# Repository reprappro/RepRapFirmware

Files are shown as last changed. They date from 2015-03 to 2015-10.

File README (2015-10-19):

This firmware is intended to be a fully object-oriented highly modular control program for
RepRap self-replicating 3D printers.

It owes a lot to Marlin and to the original RepRap FiveD_GCode.

This is the version for the RepRap Duet: 

  http://blog.think3dprint3d.com/2013/12/Duet-Arduino-Due-compatible-3DPrinter-controller.html  

To edit and compile this you will also need the Arduino board files from

  https://github.com/reprappro/RepRapFirmware/tree/master/Hardware

A complete uploadable executable version is in the directory Release/RepRapFirmware.bin in this
repository.  For details of how to flash it to a Duet see here:

  https://reprappro.com/documentation/commissioning-introduction/maintenance-duet/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

For details of how to compile the source code, see below.

General design principles:

  * Control by RepRap G Codes.  These are taken to be machine independent, though some may be unsupported.
  * Full use of C++ OO techniques,
  * Make classes hide their data,
  * Make everything except the Platform class (see below) as stateless as possible,
  * No use of conditional compilation except for #include guards - if you need that, you should be
       forking the repository to make a new branch - let the repository take the strain,
  * Concentration of all machine-dependent definitions and code in Platform.h and Platform.cpp,
  * No specials for (X,Y) or (Z) - all movement is 3-dimensional,
  * Except in Platform.h, use real units (mm, seconds etc) throughout the rest of the code wherever possible,
  * Try to be efficient in memory use, but this is not critical,
  * Labour hard to be efficient in time use, and this is critical,
  * Don't abhor floats - they work fast enough if you're clever,
  * Don't avoid arrays and structs/classes,
  * Don't avoid pointers,
  * Use operator and function overloading where appropriate.

Naming conventions:

  * #defines are all CAPITALS_WITH_OPTIONAL_UNDERSCORES_BETWEEN_WORDS
  * No underscores in other names - MakeReadableWithCapitalisation
  * Class names and functions start with a CapitalLetter
  * Variables start with a lowerCaseLetter
  * Use veryLongDescriptiveNames

Structure:

There are nine main classes:

  * RepRap
  * GCodes
  * Heat
  * Move
  * Platform
  * Network
  * Webserver
  * Roland, and
  * PrintMonitor

RepRap:

  This is just a container class for the single instances of all the others, and otherwise does very little.

GCodes:

  This class is fed GCodes, either from the web interface, or from GCode files, or from a serial interface,
  Interprets them, and requests actions from the RepRap machine via the other classes.

Heat:

  This class implements all heating and temperature control in the RepRap machine.

Move:

  This class controls all movement of the RepRap machine, both along its axes, and in its extruder drives.

Platform:

  This is the only class that knows anything about the physical setup of the RepRap machine and its
  controlling electronics.  It implements the interface between all the other classes and the RepRap machine.
  All the other classes are completely machine-independent (though they may declare arrays dimensioned
  to values #defined in Platform.h).

Network:

  This class implements a basic TCP interface for the Webserver classes using LWIP.

Webserver:

  This class talks to the network (via Platform) and implements a simple webserver to give an interactive
  interface to the RepRap machine. It uses the Knockout and Jquery Javascript libraries to achieve this.
  In addition, FTP and Telnet servers are provided for easier SD card file management and G-Code handling.

Roland:

  This class can interface with a Roland mill (e.g. Roland MDX-20/15) and allows the underlying hardware
  to act as a G-Code proxy, which translates G-Codes to internal Roland commands.

PrintMonitor:

  This class provides methods to obtain statistics (height, filament usage etc.) from generated G-Code
  files and to calculate estimated print end-times for a live print.

When the software is running there is one single instance of each main class, and all the memory allocation is
done on initialization.  new/malloc should not be used in the general running code, and delete is never
used.  Each class has an Init() function that resets it to its boot-up state; the constructors merely handle
that memory allocation on startup.  Calling RepRap.Init() calls all the other Init()s in the right sequence.

There are other ancillary classes that are declared in the .h files for the master classes that use them.  For
example, Move has a DDA class that implements a Bresenham/digital differential analyser.

Timing:

There is a single interrupt chain entered via Platform.Interrupt().  This controls movement step timing, and
this chain of code should be the only place that volatile declarations and structure/variable-locking are
required.  All the rest of the code is called sequentially and repeatedly as follows:

As of version 057r-dc42 the tick interrupt (which is set up by the Arduino core) is also used to set up ADC conversions,
read the result of the last conversion, and shut down heaters when temperature errors are detected.

All the main classes have a Spin() function.  These are called in a loop by the RepRap.Spin() function and implement
simple timesharing.  No class does, or ever should, wait inside one of its functions for anything to happen or call
any sort of delay() function.  The general rule is:

  Can I do a thing?
    Yes - do it
    No - set a flag/timer to remind me to do it next-time-I'm-called/at-a-future-time and return.

The restriction this strategy places on almost all the code in the firmware (that it must execute quickly and
never cause waits or delays) is balanced by the fact that none of that code needs to worry about synchronization,
locking, or other areas of code accessing items upon which it is working.  As mentioned, only the interrupt
chain needs to concern itself with such problems.  Unlike movement, heating (including PID controllers) does
not need the fast precision of timing that interrupts alone can offer.  Indeed, most heating code only needs
to execute a couple of times a second.

Most data is transferred bytewise, with classes' Spin() functions typically containing code like this:

  Is a byte available for me?
    Yes
      read it and add it to my buffer
      Is my buffer complete?
         Yes
           Act on the contents of my buffer
         No
           Return
  No
    Return

Note that it is simple to raise the "priority" of any class's activities relative to the others by calling its
Spin() function more than once from RepRap.Spin().

-------------

Compiling from Source

Although the firmware was originally developed using Eclipse Juno, the latest version of the Arduino toolkit (1.6.4) breaks compatibility
with the Arduino Eclipse Plugin. Hence a Makefile has been introduced to compile the firmware easily on OS X and Linux. For Windows there
is also a Windows PowerShell script available.

As a prerequisite you must install Arduino IDE and the necessary board files. Refer to the README file in the Hardware directory for
basic instructions on how this can be achieved.

Compiling the firmware is fairly easy on *nix-based operating systems. All you need to do is to run

  make all

in the source code folder. On Windows, you can use the corresponding PowerShell script instead:

  powershell.exe -ExecutionPolicy Unrestricted -FileName .\Make.ps1

Once a firmware binary has been generated, both Makefiles can be further used to upload the generated output file to the erased electronics
board:

  make upload

or on Windows

  powershell.exe -ExecutionPolicy Unrestricted -FileName .\Make.ps1 upload

In order to take advantage of more sophisticated development conditions, a clang configuration file is included in this directory. It may be used,
for example, with vim-clang. If you decide to use it, just don't forget to set your clang C options to '-std=gnu99' and your CPP flags to '-std=gnu++11'.

-------------
Note on dc42 fork of this firmware:

As well as containing various bug fixes and performance improvements, I have added various functionality compared to the original RepRapPro version.
The major changes are:

- Z probe reading is included in the web server poll response
- Homed status (i.e. whether homes since reset) is maintained for all 3 axes and included in the web server poll response
- Once the X and Y axes have been homed, movement is limited to the range of the axis, except when the G0 or G1 command includes
  the check endstops (S1) parameter. Use the M208 command to set axis travel if the default values in the firmware are incorrect for your machine.
- Implemented M301 (hot end PID parameters) and M304 (bed PID parameters) commands. Extended these commands to allow setting of thermistor
  resistance at 25C (R parameter) and thermistor beta (B parameter). A negative P parameter means don't use PID, use bang-bang control.
- Implemented M999. This resets the Duet.
- Added temperature (T) and temperature coefficient of height (C) parameters to the G31 command
- Added support for modulated IR sensor (M558 P2) and ultrasonic sensor (M558 P3)
- Various parameters are now saved to flash memory (Z-probe parameters, network parameters, PID parameters)
- FAN0 line is driven at 25kHz and pin 25 on the expansion header (Duet) can utilise the tacho line of 4-pin PWM fans

-------------
Note on zpl fork of this firmware:

Based on dc42's long-time proven Duet firmware fork, I have implemented a couple more features and (partially) merged in features from RepRapPro's development firmware branch.
The most significant changes are:

- FTP and Telnet support
- Reliable low-level networking and implementation of the internal EMAC ISR
- Internal G-Code queuing to execute non-movement codes just-in-time and not ~20 moves too early (due to the look-ahead)
- M25: SD-card prints are paused as soon as the current move finishes
- M0 does no longer disable any stepper motors or heaters if the print is paused. This shall simplify print restarts (requires my web interface fork)
- Implemented cold retracts, minimum temperature is 90C
- Flash usage is optional; only one line needs to be commented out to disable it

See the "Changes in ... fork" text files for complete lists of all the changes dc42 and zpl have contributed.

-------------

Version 1.09

Started: 2012-11-18
This README dated: 2015-10-14

Adrian Bowyer
RepRap Professional Ltd
http://reprappro.com

Licence: GPL

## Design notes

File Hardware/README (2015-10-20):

Custom hardware tree for the Duet platform (version 1.0.4)

This tree is based upon the official "Arduino Due" 1.6.5 platform files, however the following changes were made:

- WString class is no longer present in the Arduino core. Use char arrays in conjunction with StringRef containers instead
- EMAC RX buffers were increased to 128*32 for optimal network performance
- UART classes were expanded by a "canWrite" method for better sending performance

To include this hardware tree, open the Arduino IDE.  Open the Boards Manager and install the Due device tree.  Then
go to File -> Preferences and set "Additional Boards Manager URLs" to:

  https://github.com/reprappro/RepRapFirmware/raw/dev/Hardware/package_reprap_index.json
  
Then open the Boards Manager and install the Duet device tree.

All of these files are licensed under the terms and conditions of the GPL.

Many thanks to David Crocker aka dc42 for providing the initial Arduino core patches
and to Tony@T3P3 for providing the necessary changes for their new Duet 0.8.5!

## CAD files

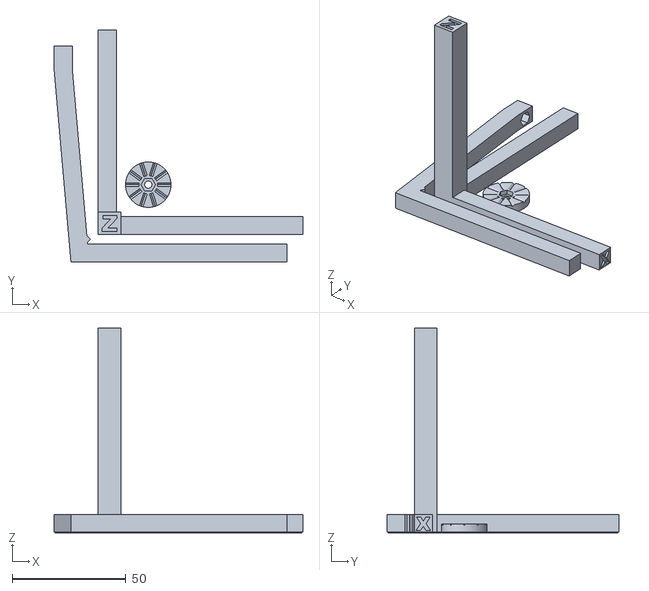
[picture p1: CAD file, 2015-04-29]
STL/calibration_90mm.stl
109.4 x 102.0 x 90.0

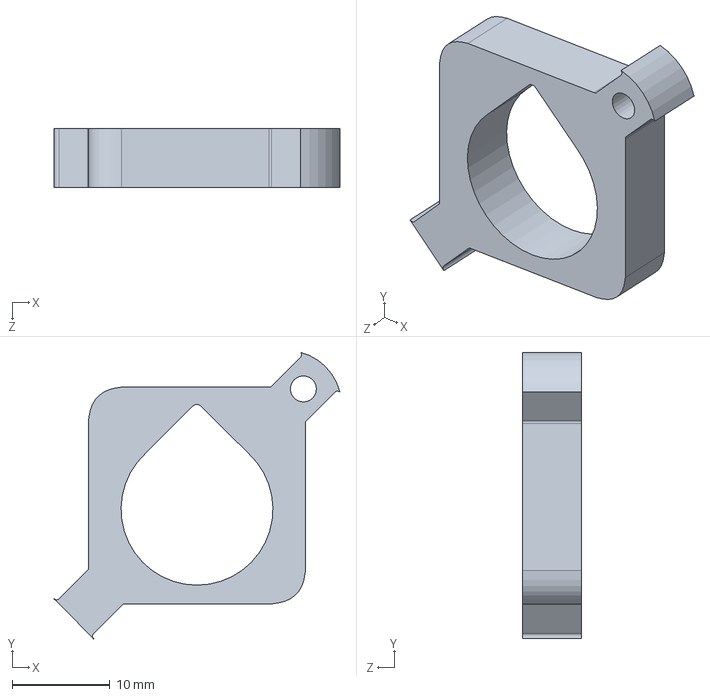
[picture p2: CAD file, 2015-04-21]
STL/Dual-colour-logo-keyring/rrp-logo-block.SLDPRT
29.3 x 29.3 x 6.00 mm

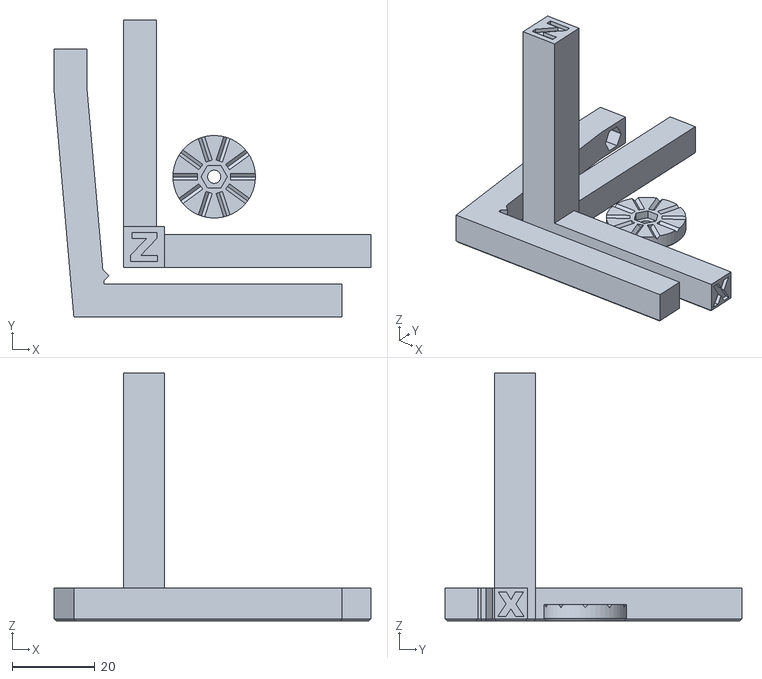
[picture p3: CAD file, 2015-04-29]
STL/calibration_60mm.stl
76.8 x 72.0 x 60.0

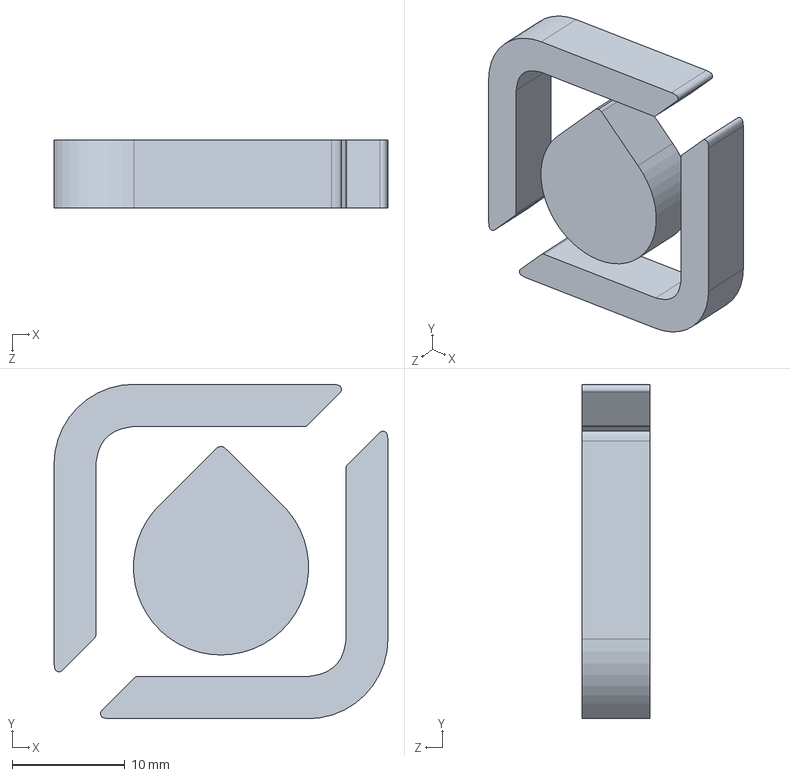
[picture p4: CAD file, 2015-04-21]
STL/Dual-colour-logo-keyring/rrp-logo.SLDPRT
29.6 x 29.7 x 6.00 mm

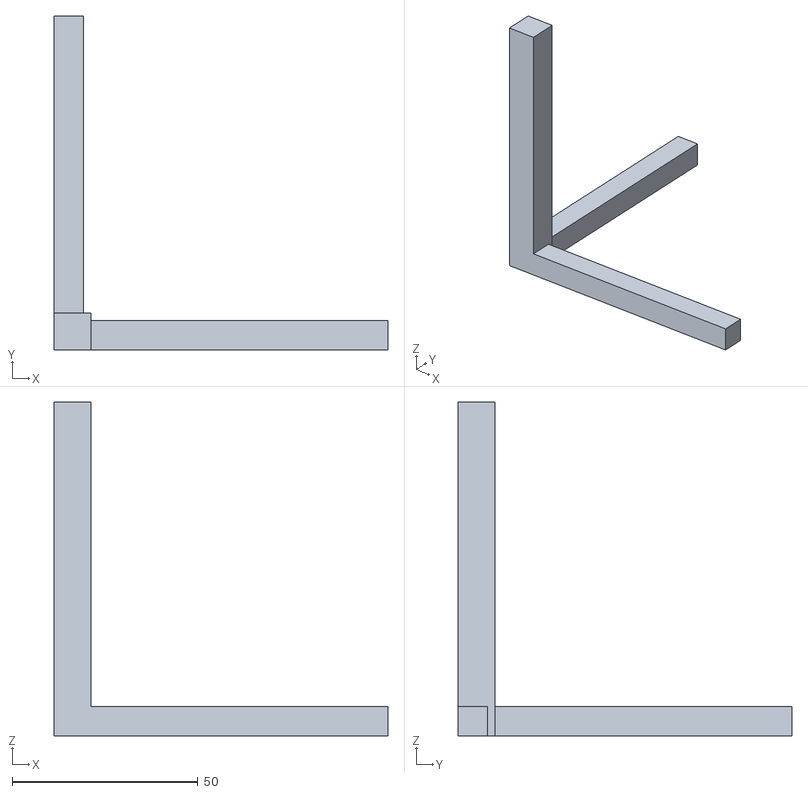
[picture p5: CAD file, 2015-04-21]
STL/testpiece_90mm.stl
90.0 x 90.0 x 90.0

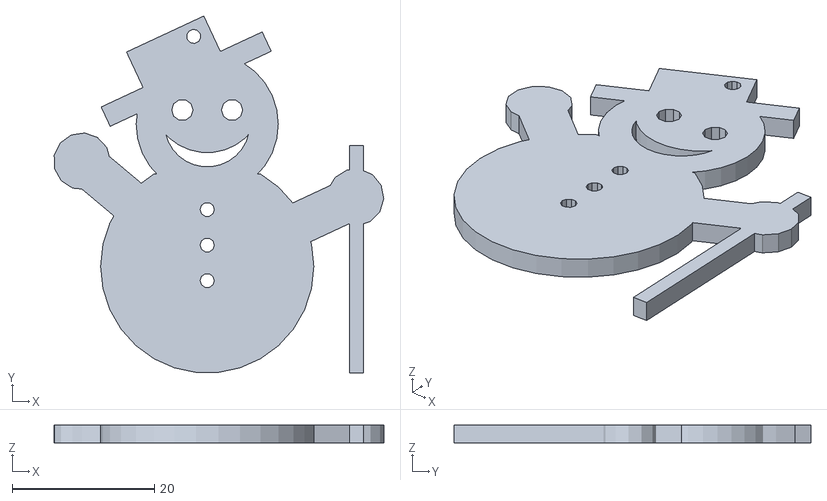
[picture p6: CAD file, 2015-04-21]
STL/Snowman.stl
46.4 x 50.2 x 2.50

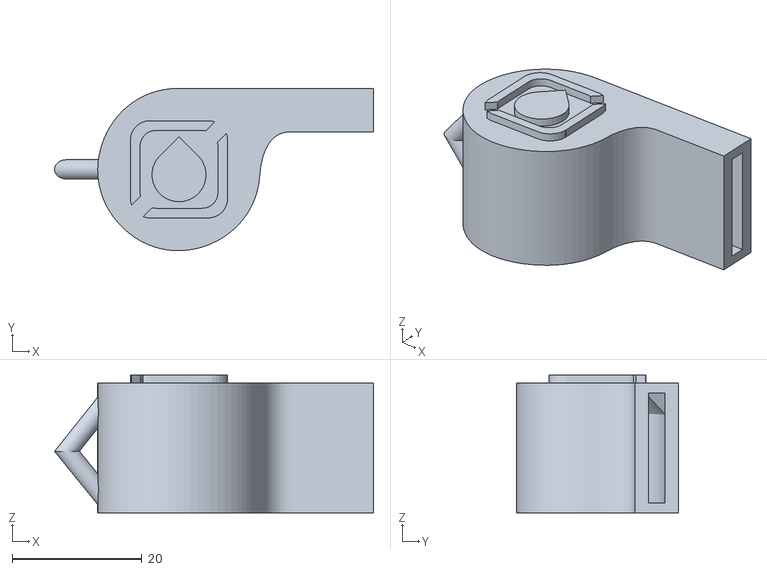
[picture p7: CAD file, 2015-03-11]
STL/Whistle.stl
49.2 x 25.0 x 21.2

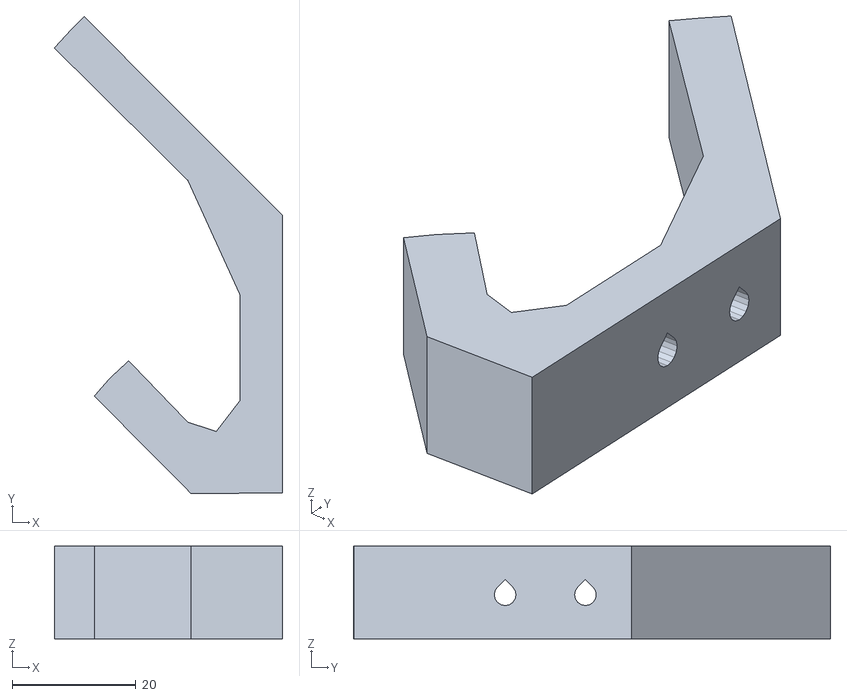
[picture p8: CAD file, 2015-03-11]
STL/CoatHook.stl
36.9 x 77.1 x 15.0

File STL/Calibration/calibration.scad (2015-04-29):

// OpenSCAD file for producing the testpiece, gauge and thumbwheel for orthogonal axis compensation for RepRapPro Ormerod, Mendel and Huxley printers //
// Revised with text. You need to use OpenSCAD version 2015.03 for the test to render correctly, and Arial Black installed as a font //

long = 90; // Set length for testpiece here
chamfer=0.5;

// comment out the following lines to get the parts you want. Comment out the translations if you want the part at the origin.

Gauge();

translate ([12,12,0])
TestPiece();

translate ([34,34,0])
ThumbWheel();



module Gauge()
{
    union()
     {
         chamfer_cube(long+5,8,8);
         translate([5, 10, 4]) rotate([0,0,45]) chamfer_cube(5,5,8,ctr=true);
         
         difference ()
         {
             rotate([0,0,5]) chamfer_cube(8,long,8);
             translate ([-sin(5)*(long-5)-1,(long-5),-1]) cube([10,11,10]);
         }
         
         translate ([-sin(5)*(long-5),(long-5),0]) difference ()
         {
             chamfer_cube(8,10,8,x1=false);
             translate([4,5,4]) rotate([0,90,0]) cylinder(r=1.6,h=10,center=true,$fn=30);
             translate([4,5,4]) rotate([90,0,90]) cylinder(r=3.2,h=6,center=false,$fn=6);
         }
     }
}

module ThumbWheel()
{
	difference()
	{
		intersection ()
		{
			cylinder(r=10,h=4,center=false,$fn=50);
			cylinder(r1=10-chamfer,r2=10+4-chamfer,h=4,center=false,$fn=50);
		}
		translate ([0,0,-1]) cylinder(r=1.6,h=6,center=false,$fn=30);
		translate ([0,0,-0.02]) cylinder(r1=1.6+chamfer,r2=1.6,h=chamfer,center=false,$fn=30);
		translate([0,0,2]) cylinder(r=3.2,h=3,center=false,$fn=6);

		for(a = [0 : 36 : 360] )
		{
		rotate([0,0,a]) translate([4,0,3.2]) rotate([45,0,0])
            cube([7,1.5,1.5]);
		}
	}
}


module TestPiece()
{
 union()
 {
	difference ()
     {
         chamfer_cube(long,8,8);
         translate ([long-1,0.75,1]) rotate ([90,0,90]) 
         linear_extrude(height = 1.1) text("X", font="Arial Black", size=6);
     }

	difference ()
     {
         chamfer_cube(8,long,8);
         translate ([0.75,long+0.1,1]) rotate ([90,0,0]) 
         linear_extrude(height = 1.1) text("Y", font="Arial Black", size=6);
     }

	difference ()
     {
         chamfer_cube(10,10,long);
         translate ([1.5,1.5,long-1]) 
         linear_extrude(height = 1.1) text("Z", font="Arial Black", size=7);
     }


 }
}

module chamfer_cube (x,y,z,h=chamfer,ctr=false,x1=true,x2=true,y1=true,y2=true)
{
    dh = sqrt(2*pow(h,2));

	if (ctr==true)
    {
        translate ([-x/2,-y/2,-z/2]) difference ()
        {
            cube([x,y,z]);
            if (x1==true) {translate([x/2,-0.02,-0.02]) rotate ([45,0,0]) cube([x+1,dh,dh],center=true);}
            if (x2==true) {translate([x/2,y+0.02,-0.02]) rotate ([45,0,0]) cube([x+1,dh,dh],center=true);}
            if (y1==true) {translate([-0.02,y/2,-0.02]) rotate ([0,45,0]) cube([dh,y+1,dh],center=true);}
            if (y2==true) {translate([x+0.02,y/2,-0.02]) rotate ([0,45,0]) cube([dh,y+1,dh],center=true);}
        }
    }
    else
    {
        difference ()
        {
            cube([x,y,z]);
            if (x1==true) {translate([x/2,-0.02,-0.02]) rotate ([45,0,0]) cube([x+1,dh,dh],center=true);}
            if (x2==true) {translate([x/2,y+0.02,-0.02]) rotate ([45,0,0]) cube([x+1,dh,dh],center=true);}
            if (y1==true) {translate([-0.02,y/2,-0.02]) rotate ([0,45,0]) cube([dh,y+1,dh],center=true);}
            if (y2==true) {translate([x+0.02,y/2,-0.02]) rotate ([0,45,0]) cube([dh,y+1,dh],center=true);}
        }        
	}
}

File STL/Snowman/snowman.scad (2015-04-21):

/*

Christmas Snowman

Christine Bowyer

Licence: GPL

*/

thickness=2.5;
arms=true;
union()
{
	difference()
	{
		union()
		{
			cylinder(h =thickness, r = 15,center=true);
			if(arms)
			{
				translate([21,1,0])
					cube([2,32,thickness],center=true);
				rotate([0,0,25])
				union()
				{
				translate([16,0,0])
					cube([14,6,thickness],center=true);
				translate([23,0,0])
					cylinder(h =thickness, r = 4,center=true);
				}
				rotate([0,0,140])
				union()
				{
				translate([16,0,0])
					cube([14,6,thickness],center=true);
				translate([23,0,0])
					cylinder(h =thickness, r = 4,center=true);
				}
			}
		}
		translate([0,15,0])
			cube([20,4,2*thickness],center=true);
		for ( i = [-1 : 1] )
			translate([0,3+5*i,0])
				cylinder(h=20, r=1, center=true,$fn=10);
	}
	translate([0,20,0])
	difference()
	{
		union()
		{		
			cylinder(h =thickness, r = 10,center=true);
			rotate([0,0,25])
			difference()
			{
			translate([0,10,0])
			union()
			{
				cube([12,8,thickness],center=true);
				translate([0,-3,0])
					cube([25,3,thickness],center=true);
			}
			translate([3.5,12,0])
			cylinder(h=20, r=1, center=true,$fn=10);
			}
		}
		
		translate([3.5,2,0])
			cylinder(h=20, r=1.5, center=true,$fn=10);
		translate([-3.5,2,0])
			cylinder(h=20, r=1.5, center=true,$fn=10);
	
		difference()
		{
			cylinder(h =20, r = 6,center=true, $fn=30);
			translate([0,4,0])
					cylinder(h=20, r=8, center=true,$fn=30);
		}
	}
}

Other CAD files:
STL/Dual-colour-logo-keyring/rrp-logo-block.stl
STL/Dual-colour-logo-keyring/rrp-logo.amf
STL/Dual-colour-logo-keyring/rrp-logo.stl
STL/calibration-60mm.stl
STL/calibration-90mm.stl

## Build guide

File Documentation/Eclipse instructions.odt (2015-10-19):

How to set up Eclipse to compile RepRapFirmware

1. Install the latest Arduino IDE (1.6.4+) and Eclipse (Luna)
2. Start „Arduino IDE“, go to „File → Preferences“ and set content of the text box „Additional Boards Manager URL“ to:
  https://github.com/chrishamm/RepRapFirmware/raw/dev/Hardware/package_reprap_index.json
3. Confirm your changes by clicking on „OK“ and go to „Tools → Board: … → Boards Manager“. Once you're there, you need to install two board packages:
  1) Arduino SAM boards (32-bits, ARM Cortex-M3)
  2) Duet platform
4. If you haven't done so already, download a copy of the latest RepRapFirmware and unpack it
5. Copy „RepRapFirmware.cpp“ and „RepRapFirmware.h“ to a temporary location, you will need them later on
6. Open Eclipse and create a new workspace
7. Install the Arduino Eclipse Plugin

a) Go to „Help → Install New Software“

b) Add a new repository „Arduino Eclipse Plugin (Nightly)“ with this URL:

http://eclipse.baeyens.it/nightly

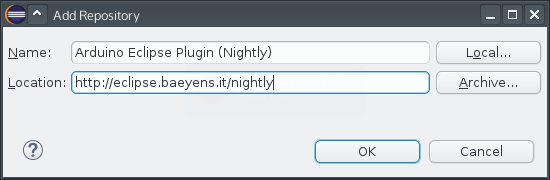
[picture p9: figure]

c) Untick „Group Items“ and check „Arduino eclipse extensions“ in the list:

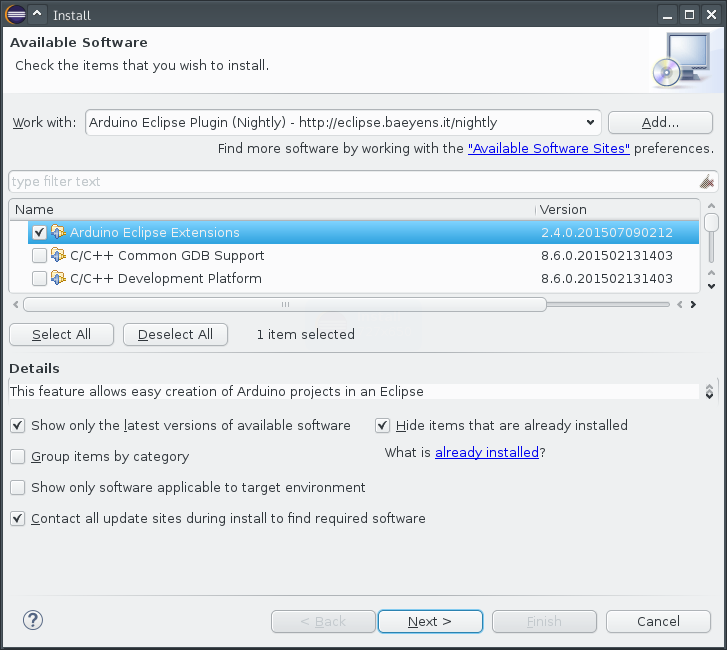
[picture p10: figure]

d) Finish the wizard

e) When asked to trust an unknown certificate, select it from the list and

confirm this exception by clicking on „OK“

e) Restart Eclipse

8. Create a new Arduino sketch:

a) Go to „File → New → Project“ and select „Arduino → New Arduino

sketch“

b) Call it „RepRapFirmware“ and set the location to the directory of your

RepRapFirmware copy

c) For your „Boards.txt file“ you need to select the one having „RepRap“ in

its file path. On Linux, it will look like this:

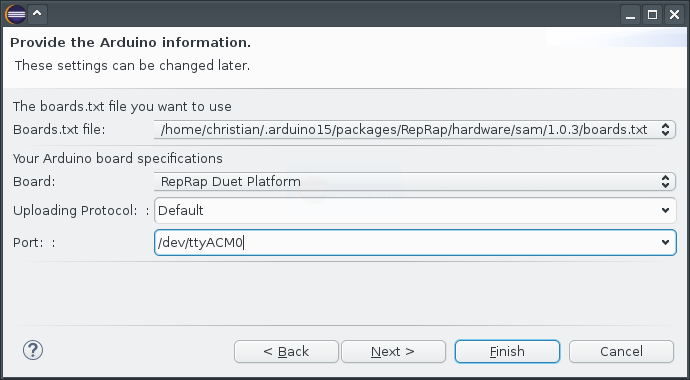
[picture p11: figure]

d) Check your source code directory for the following files or directories:

- .cproject

- .project

- .settings

- arduino

If any of them is present, it is highly recommended to delete them before

you continue

e) Finish this wizard

9. Overwrite „RepRapFirmware.cpp“ and „RepRapFirmware.h“ with the two files that you backed up earlier
10. Right click on „Hardware“ and go to „Resource Configurations → Exclude from build“. Then click on „Select all“ confirm your input
11. Right-click on the „RepRapFirmware“ directory in the Project Explorer and go to „Properties → C/C++ General → Paths and Symbols“
12. There you must to add four include directories as seen in the following screenshot. On Windows, the Arduino packages directory can be found in %APPDATA%\Arduino15 and on OS X, it is $HOME/Library/Arduino15.

Make sure you have „Add to all languages“ checked while adding them!

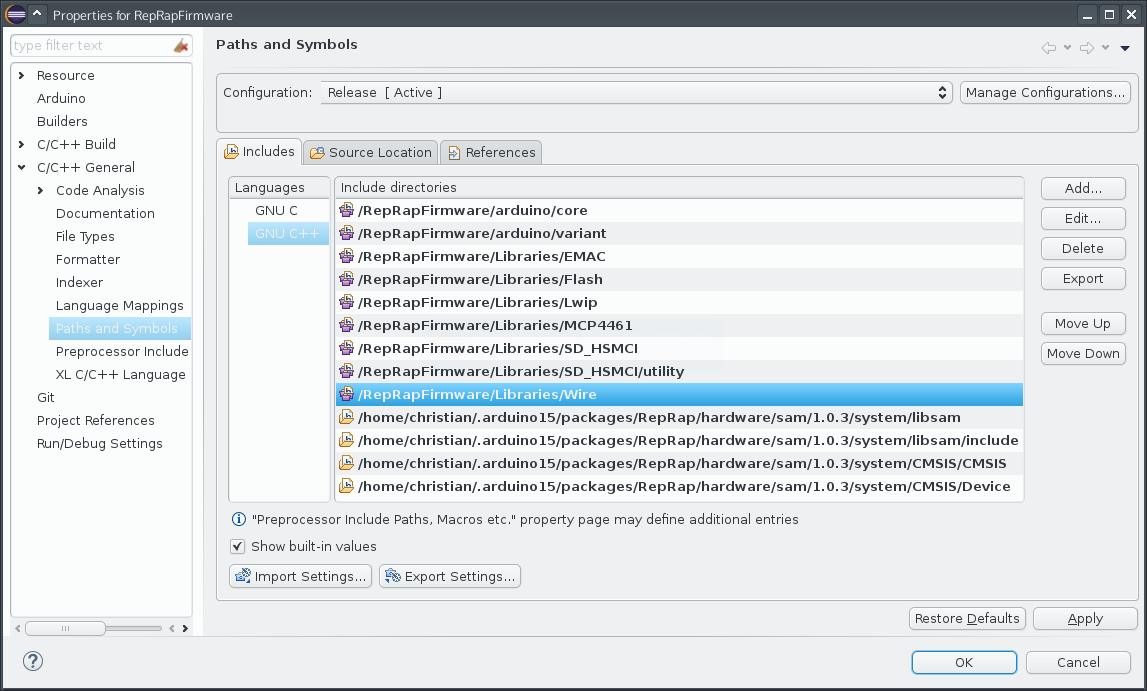
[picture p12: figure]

13. Press „OK“ and confirm the message prompt asking you to rebuild the search cache
14. Select an arbitrary file in the Project Explorer and click on „Verify“ () in the Arduino toolbar to build the firmware. Once everything has been compiled, you can find a new firmware binary in the Release directory

NOTE: Please be aware that this guide advises the use of nightly Arduino Eclipse Plugin builds, because no stable version for Arduino 1.6.4+ was available at the time of writing. For that reason you may see more error/warning messages than you would if you were using only the supplied Makefile.

** Your mileage may vary !

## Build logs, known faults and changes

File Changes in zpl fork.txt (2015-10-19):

Additional features in comparison to dc42's and/or RRP's official firmware:

* Cooling support: M106 can invert PWM cooling if "I1" is passed to it once (required for a 4-pin PWM fan)

* EMAC: Interrupt-driven input and optimized output mechanism

* FTP server support with long file lists (up to 6KB)

* Telnet support

* Config output: M503 removes duplicate whitespaces to display the new RRP config template completely on the web interface

* Cold extrudes: M302 can allow or deny them with the "P" parameter, it reports the status if no arguments are specified

* Discrimination between cold extrudes and cold retracts for filament changing (minimum retraction temperature is 90°C)

* Z-probing: M558 can be used to specify the axes for which the Z probe will be used (e.g. M558 P1 X0 Y0 Z1 for Z-probing only)

* File information for files being printed are displayed on page reload (except for layer stats)

* Lowered minimum extrusion temperature from 170C to 160C

* Reduced Z-probe height for automatic bed compensation from 8mm to 5mm

* Added interrupt to pin 10 (Duet) / pin 18 (Duex4) on the expansion header for 4-pin PWM tacho line (can be viewed with my web interface)

* Firmware binaries are built with -O3 optimization enabled

* File information can be retrieved from G-Code files generated by common slicers (Slic3r, Cura and S3D)

* When axes are being homed and axis drives are disabled, the according homing states are reset

* If the print was paused, M0 will neither deselect the current tool nor turn off any heaters
  Use my web interface fork (version 1.08+) to restart failed prints easily on demand

* M0 puts drives into idle state, M1 turns them off (thanks dc42)

* M0 and M1 run stop.g and sleep.g before everything is switched off

* Ability to specify which drives may be disabled by M18 and M84

* Buffered G-codes are enqueued if moves are being performed to ensure all codes are executed just-in-time

* When prints are paused, movement stops as soon as the current move has finished

* When prints are either being stopped or resumed, macro files (pause.g or resume.g) are executed

* Implemented 'R' paramter for G0/G1 to be able to go to the coordinates a print was initially paused at

* default.g is executed if config.g cannot be found (same behaviour as with versions older than 0.90)

* config.g has been removed from the SD-image directory, copy default.g to create it

* Z-probe modulation pin may be set using M558 'R' parameter (thanks dc42)

* X-axis direction remains compatible with prior releases, meaning all stepper motor connectors on a Duet v0.6 are connected the same way round.
  This was changed once more with RRP's dev FW 0.90 and their official 0.78 FW, however my Ormerod 1 "default.g" file has been updated to compensate this

* Total extruder positions since power up, last G92 or last M23 are reported to the web interface.
  This includes raw extruder positions without the extrusion multipliers applied to them, to improve filament estimation (requires web interfacae version 1.06+ to work)

* Current fan value is reported by M106 and included in the web interface status response

* Added 'R' parameter to M106 to restore the last-known fan value after it has been turned off. It may also be used to maintain this value

* Implemented M500, M501 and M502 (EEPROM tools) and made Flash usage optional when building the firmware.
  Passing 'S1' to M501 will enable auto-save for non-volatile parameters, so backward compatibility with forks based on dc42's firmware can be maintained.

* Implemented M32 (Select file and start SD print)

* Print status is not changed when a macro file is being executed unless it's part of a real G-Code file

* New-style JSON status and config responses (see http://reprap.org/wiki/Proposed_RepRap_Duet_Status_Responses) including firmware-based print end-time estimations

* Move class can perform isolated moves (without the look-ahead ring) when a print has been paused

* Firmware can be built using a custom Arduino device tree (see Data/Firmware build instructions.odt)

* Bug fix: Old-fashioned G32 call (without macro utilisation) initially resets bed compensation parameters

* Bug fix: Actual extruder positions are reported instead of the internal ones from the GCodes class

* Bug fix: Layer height and filament usage for web interface are read from both start and end of a gcode file

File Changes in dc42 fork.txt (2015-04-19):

Additional functionality in 0.78u-dc42 release compared to RRP 0.78a:

* The Duet can serve all the files needed by the web interface

* All ADC readings are done in the tick ISR to avoid the processor having to wait for ADC conversions and provide faster thermistor and z-probe response.

* Additional over-temperature protection is done in the tick ISR, and the watchdog timer resets the system if the tick interrupt fails.

* A software watchdog is used to reset the processor if it gets stuck in a spin loop.

* Printing doesn't hang if the USB port is disconnected (or attached PC goes to sleep) during a print.

* The number of bits of temperature resolution is increased from 10 to 13 (i.e. 12-bit ADC + 1-bit oversampling) to increase the temperature resolution

* ADC corrections can be set in the M305 command.

* M208 command allow you to set axis minimum positions (e.g. negative x-axis position) as well as maximum positions.

* G1 commands with S1 parameter (i.e. seeking for endstops) do not need to be followed by a G92 command to work properly. The positions assumed to have been reached when endstops are hit are those set by the M208 command.

* Long filename support for files on the SD card

* The limit of 42 files in the list of gcode files on the SD card is removed (but there is still a limit of 2000 characters)

* M220 (set speed factor override) and M221 (set extrude factor override) commands are supported.

* Option to invert cooling fan PWM

* Additional z-probe type 3 is supported, for z-probe boards that incorporate more than one type of z-probe (e.g. my hot end boards)

* Separate G31 parameters can be saved for z-probe types 0, 1/2, and 3

* Various parameters (G31 values, IP address, MAC address, thermistor parameters, PID parameters) are saved to flash memory (note that these values do not survive a firmware upgrade)

* M122 diagnostics command shows additional parameters such as bed compensation heights, last reset reason, and up-time

* When pausing a print from SD card, if the printer is executing a 'wait' command such as M116, control is returned to the web interface immediately, without waiting for the command to complete (which could take a long time).

* The USB port is responsive immediately after power up or reset even when no Ethernet cable is connected

* A new file upload protocol supports much faster uploading of any type of file, without a limit on line length, with error reporting, and with a check that the file length is correct when the upload is complete.

* The web interface can now request the status of a file. This returns information such as layer height, object height, and filament required. These parameters are useful in displaying print progress and estimating time to completion of a print. Gcode files generated by slic3r, Cura and Simplify3D are supported.

* M80 and M81 ATX power on/off commands are supported

* M999 software reset command is supported

* M301 and M304 commands to set PID parameters now take an additional T parameter. This should be set to the approximate extra PWM value needed (on a scale of 0 to 255) per extra degC of temperature. It is used to preset the I-term to a suitable value when PID kicks in, to enable fast heating with minimum overshoot.

* M301 and M304 commands to set PID parameters now take an additional S parameter. This allows for variations in cartridge heater power and supply voltage to be taken into account more easily.

* M0 and M1 commands now turn all heaters off instead of setting them to their standby temperatures

* M0 no longer disables drives or resets the 'homed' status. M1 still does.

* When using a Z probe, Z homing and bed probing are done in two stages (a fast stage followed by a slow stage) for better accuracy.

* The default initial Z homing and bed probing speed has been increased. This is possible because Z homing and bed probing slow down when the probe reading is approaching the target value.

* M116 takes an optional P parameter to specify which tool to wait for. If no P parameter is given, it waits for all tools and the bed as before. The main purpose of this is that on a tool change, you can wait for the new tool to heat up to operating temperature but not wait for the old tool to cool down to standby temperature.

* When fetching file info, if the gcode file contains more than one 'filament used' comment, the filament lengths in all of them are returned to the web interface

* The active and standby temperatures of all heaters are included in the status poll response

* The M220 and M221 commands now return the override factors if no S parameter is provided

* Temperature errors are reported to the web server as well as to the USB interface

* The Heat section of the M122 diagnostics report now shows the accumulated PID I-term

* G90 and G91 commands now affect only the the axes, not the extruders

* M563 command extended to allow the tool number origin to be adjusted. This is to permit multi-media gcode files generated by slic3r 1.17 to be printed. If there is no P parameter in the command then the S parameter specifies an offset to be added to tool numbers in T, G10, M104 and M109 commands. This is so that multi-media gcode files generated by slic3r can be printed without having to edit all the tool numbers in the gcode file first. This extension is intended to be temporary, until slicer provides a mechanism for specifying the tool numbers. A separate offset is maintained for each data source (USB, web or SD card) and the offset for data from the SD card is reset to zero when a new file is started. To use this facility to print slic3r multi-media gcode files, add M563 S1 to your start gcode.

* M104 and M109 commands now accept an optional T parameter to specify the tool number, as generated by slic3r in multi-media gcode files.

* Movement code from RepRapPro's 0.89 dev version incorporated, including 5-point manual or automatic bed compensation mechanism. Fixed a bug that caused the head to try to move beyond the axis limits when 5-point auto compensation was used and G32 was executed more than once.

* Heater status (off/standby/on/fault) is included in the status poll response for the web interface

* Incorporated code from RepRapPro 0.89 dev version to allow many more M-commands to return the existing values as well as set them.

* Incorporated code from RepRapPro 0.89 dev branch to implement the M119 and M135 commands. Fixed a bug in the M135 (set heat sample interval) command, which meant that if you changed the interval from its default value of 0.5 seconds, you needed to adjust the I parameter by the same ratio and the D parameter by the inverse ratio.

* Extrusion totals are reset to zero when starting a new print from SD card.

* If a Pause (M25) command is received when the machine is executing a Dwell command or a command that waits for temperatures to be reached, the command is interrupted immediately so that the pause takes immediate effect. The interrupted command will be completed if the print is resumed.

* The G10 command can now be used to specify nozzle offsets (as well as active/standby temperatures)

* FTP server supported (thanks zombiepantslol)

* Telnet server supported (thanks zombiepantslol)

* Fan RPM supported (thanks zombiepantslol)

* Interrupt-driven network timing to better handle slow writes to SD card (thanks zombiepantslol)

* M18 and M84 now allow selective disabling of drives (thanks zombiepantslol)

* Bug fix: uploading file whose name includes an uppercase G now works. Similarly for setting a machine name containing an uppercase G (M550) or password containing an uppercase G (M551)

* Bug fix: if the machine name in an M550 command is followed by a tab character, then the name is assumed to terminate just before the tab character. Similarly for passwords set using M551.

* Bug fix: setting a machine name that contains a quote or backslash character no longer causes the webserver to return a bad JSON response in response to the rr_name request

* Bug fix: indentation of multipart messages sent to the USB interface now works properly

* Bug fix: if G10 was used to set just the active temperature for a tool, then the standby temperature for the same tool was set to an undefined value, and vice versa

* Bug fix: if bed compensation or axis compensation was in use, then a G1 S1 command to home an axis could be prematurely terminated if the head was already at the endstop position for a different axis

* Bug fix: if a tool was defined as using zero drives or zero extruders, it would be treated as assuming a collection of drives or extruders according to the values in an uninitialised array

* Bug fix: the cumulative extruder positions were getting reset (typically to zero) on a tool change or other macro file execution

* Bug fix: numerous calls to strncat were being made with a 'nchars' parameter that was larger than space available in the destination buffer

* Bug fix: print moves received just prior to an M109 or M190 command were not executed until after the heater had reached temperature instead of before

* Bug fix: if the last command in a macro file did not have a newline character at the end then the command might not be fully executed

* Bug fix: the cooling fan PWM frequency was set to a frequency that was much too high for the mosfet to handle. It has been changed to 25kHz so that it can be used to control 4-wire PWM fans meeting the Intel specification.

* Bug fix: homing the Z axis or doing bed probing when axis compensation was enabled caused the X and Y origins to move, often by several mm

* Bug fix: the M92 command could not be used to set extruder steps/mm in machines with multiple extruders unless either only one extruder steps/mm value was supplied (which was applied to all extruders) or 5 extruder steps/mm values were supplied 

Additional functionality in web interface 1.03 compared to RRP 0.65:

* Faster (>6Mbytes/min), more reliable file uploading, with reporting and graceful recovery if an upload fails

* All web files and config files can also be uploaded

* More accurate (usually!) estimate of print completion time, based on filament consumption

* The machine name is displayed

* The filament requirement and object height are fetched automatically from the SD card file being printed, for use in estimating the completion time

* Works with FireFox as well as Chrome

* "Upload & Print" button (replaces direct web print button, uploads to the SD card first for more reliable printing)

* The extruder position box reports total filament extruded, instead of the amount extruded in the last move

* Additional status Halted is shown (if emergency stop has been used) as well as Ready and Active

* The Print Status tab includes slider controls to allow the speed and extrusion factors to be adjusted during printing

* A second heated print head is supported

* The active and standby temperature settings of each print head, and the active temperature setting of the bed, are displayed along with the current temperature. The active and standby temperatures can both be set.

* The status of each heater (off/standby/active/fault) is displayed.

* If a browser session is reconnected while a print is in progress, the print status is retrieved and displayed.

* The cooling fan RPM is displayed (if available)

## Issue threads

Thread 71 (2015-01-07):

Z axis hangs while printing

gonAlonso, 2015-01-07:
Hello
Every time I print an object, the Z axis motor hangs after 1st print layer. I mean, it starts printing at first_layer_height, when moving on to the second one, it tryes to move, I hear it, but it barely moves. The funny is, I can move it through the web interface buttons, or sending g-codes. I've forced it to the maxSpeed (G1 Z20 F5000) and it works seamlessly. It looks like it doesn't compute acceleration the way it should. I've been browsing the reppo, the web, forums, and no solution by now.
I'm using version 0.78y-dc42, is there an updated version?
Thks

RRP-support, 2015-01-07:
This is an automated reply to your message "[RepRapFirmware] Z axis hangs while printing (#71)" sent to support@reprappro.com.

Dear gonAlonso <notifications@github.com>

Thank you for your email. We endeavour to answer all emails within 24 hours. It may take longer during busy times, and holiday periods. We process all customer queries on a first come first served basis, during our office hours which are 9am to 5pm GMT Mon-Fri.

Other support channels are available. Please refer to the relevant troubleshooting guide for your machine:

Ormerod 2: https://reprappro.com/documentation/ormerod-2/troubleshooting/
Ormerod: https://reprappro.com/documentation/ormerod/troubleshooting/

Huxley Duo: https://reprappro.com/documentation/huxley-duo/troubleshooting/
Huxley: https://reprappro.com/documentation/huxley/troubleshooting/

Mono and Tricolour Mendel: https://reprappro.com/documentation/mendel-tricolour/troubleshooting/

Support is also available from other owners of RepRapPro and other 3D printers, either through the RepRap Forums: https://forums.reprap.org or through IRC which can be accessed from here: https://reprappro.com/support-channel/ (works on Chrome, not Firefox).

Best regards,

RepRapPro Support Team.

RRP-support, 2015-01-09:
You're using dc42's version of the firmware, not this ours, so I don't know if that is causing the problem. Try reverting to the standard firmware (0.78c), using the default config.g, and see if you can recreate the problem. I would expect that you have your Z axis max speed or acceleration set too high; we have reduced it, with the following lines in config.g:

M201 X500 Y500 Z15 E500 ; Accelerations (mm/s^2)
M203 X15000 Y15000 Z100 E3600 ; Maximum speeds (mm/min)
M566 X1200 Y1200 Z30 E1200 ; Minimum speeds mm/minute

Try these settings.

Ian
RepRapPro tech support

gonAlonso, 2015-01-11:
Thank you so much for your reply, Ian.
It happens to be the same problem with the standard 78c FW. I've tested previous versions too without success.
The curious thing is, it worked nice from two weeks, but now Z axis stopped. I've been thinking on the changes I've made, and I realized I've started using slic3r instead of cura. And I tested it now, there seems to bee an option on slic3r that mess with the firmware, and cura doesn't. Did you know about any previous case? Is it known for you? Is there something I should set/unset on slic3r?
Thank you!

RRP-support, 2015-01-11:
This is an automated reply to your message "Re: [RepRapFirmware] Z axis hangs while printing (#71)" sent to support@reprappro.com.

Dear gonAlonso <notifications@github.com>

Thank you for your email. We endeavour to answer all emails within 24 hours. It may take longer during busy times, and holiday periods. We process all customer queries on a first come first served basis, during our office hours which are 9am to 5pm GMT Mon-Fri.

Other support channels are available. Please refer to the relevant troubleshooting guide for your machine:

Ormerod 2: https://reprappro.com/documentation/ormerod-2/troubleshooting/
Ormerod: https://reprappro.com/documentation/ormerod/troubleshooting/

Huxley Duo: https://reprappro.com/documentation/huxley-duo/troubleshooting/
Huxley: https://reprappro.com/documentation/huxley/troubleshooting/

Mono and Tricolour Mendel: https://reprappro.com/documentation/mendel-tricolour/troubleshooting/

Support is also available from other owners of RepRapPro and other 3D printers, either through the RepRap Forums: https://forums.reprap.org or through IRC which can be accessed from here: https://reprappro.com/support-channel/ (works on Chrome, not Firefox).

Best regards,

RepRapPro Support Team.

RRP-support, 2015-01-12:
Generally, we recommend using Slic3r. You can use Cura, but there are a few workarounds required - there is a community-created script that switches Cura from absolute to relative extrusion, and changes the Z axis so it is moved separately from X and Y, rather than all together. However, I haven't heard of such problems using Slic3r, and as this isn't normal, I don't think this is a firmware issue - it's either mechanical, or a problem with the gcode you're generating. Make sure you are using our Slic3r settings profiles - https://reprappro.com/documentation/ormerod-2/printing/#Slic3r_profiles . What happens when you try to print the test files from the SD-Image, eg snowman.g?

Ideally, please email support@reprappro.com for this issue, as I don't think it is related to firmware. This is not the best channel for receiving support; it's for reporting firmware bugs.

Ian
RepRapPro tech support

Closed 2015-01-13.

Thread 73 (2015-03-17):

Extruder not extruding 1.04 FW update

jeffreyb1004, 2015-03-17:
Extruder drive cannot be controlled in ponterface, reverting to .78c for now

RRP-support, 2015-03-17:
This is an automated reply to your message "[RepRapFirmware] Extruder not extruding 1.04 FW update (#73)" sent to support@reprappro.com.

Dear jeffreyb1004 <notifications@github.com>

Thank you for your email. We endeavour to answer all emails within 24 hours. It may take longer during busy times, and holiday periods. We process all customer queries on a first come first served basis, during our office hours which are 9am to 5pm GMT Mon-Fri.

Other support channels are available. Please refer to the relevant troubleshooting guide for your machine:

Ormerod 2: https://reprappro.com/documentation/ormerod-2/troubleshooting/
Ormerod: https://reprappro.com/documentation/ormerod/troubleshooting/

Huxley Duo: https://reprappro.com/documentation/huxley-duo/troubleshooting/
Huxley: https://reprappro.com/documentation/huxley/troubleshooting/

Mono and Tricolour Mendel: https://reprappro.com/documentation/mendel-tricolour/troubleshooting/

Support is also available from other owners of RepRapPro and other 3D printers, either through the RepRap Forums: https://forums.reprap.org or through IRC which can be accessed from here: https://reprappro.com/support-channel/ (works on Chrome, not Firefox).

Best regards,

RepRapPro Support Team.

RRP-support, 2015-03-18:
The tool number for the first hot end, set by config.g has changed, from T1 to T0. Most likely, you're sending T1 to enable the hot end, but it's actually T0 you need to send. The first extruder should be enabled by default, after reset/power on. If your gcode selects T1, it deselects the active T0 extruder. Update your gcode files and Slic3r settings so it uses T0, or change config.g so it defines the first hot end as T1.
I'm not sure if the extruder has been temperature-limited in this version of the firmware. You may need to be at extrusion temperatures to extruder. Otherwise, send M302 to allow cold extrusion.
We're investigating problems with the web interface. It appears the firmware has trouble serving the files, at times, but it's not consistent.
Ian
RepRapPro tech support

jeffreyb1004, 2015-03-19:
Sorry maybe I wasn't clear, the extrude button on pronterface is not working with this new firmware thus is not driving the filament into the bowden tube nor reversing it out. this is not limited to cold extrusions as even when up to temp ~200C it still wont manually extrude/reverse. Printing still works though. web interface seems to be consistently down i.e. I can get to the web interface, but cannot connect to the machine. It must be noted that I am bridging the connection from my laptop but since I am able to physically get to the interface, it shouldn't be an internet connection error, just a printer connection one.

RRP-support, 2015-03-19:
This is an automated reply to your message "Re: [RepRapFirmware] Extruder not extruding 1.04 FW update (#73)" sent to support@reprappro.com.

Dear jeffreyb1004 <notifications@github.com>

Thank you for your email. We endeavour to answer all emails within 24 hours. It may take longer during busy times, and holiday periods. We process all customer queries on a first come first served basis, during our office hours which are 9am to 5pm GMT Mon-Fri.

Other support channels are available. Please refer to the relevant troubleshooting guide for your machine:

Ormerod 2: https://reprappro.com/documentation/ormerod-2/troubleshooting/
Ormerod: https://reprappro.com/documentation/ormerod/troubleshooting/

Huxley Duo: https://reprappro.com/documentation/huxley-duo/troubleshooting/
Huxley: https://reprappro.com/documentation/huxley/troubleshooting/

Mono and Tricolour Mendel: https://reprappro.com/documentation/mendel-tricolour/troubleshooting/

Support is also available from other owners of RepRapPro and other 3D printers, either through the RepRap Forums: https://forums.reprap.org or through IRC which can be accessed from here: https://reprappro.com/support-channel/ (works on Chrome, not Firefox).

Best regards,

RepRapPro Support Team.

RRP-support, 2015-03-19:
We've tested this, and don't have a problem extruding from Pronterface. What Operating System are you using, and what version of Pronterface? Is it our version of Pronterface from the 'software' repository? Have you configured it correctly, ie set the length (mm to extrude), and speed (mm/s) to more than zero? What about if you send a gcode command to move the extruder, like 'G1 E10 F100'? Send M83 beforehand, to make sure the extruder is relative movement mode.
For the web interface, you need to clear the browser cache. If you've run the old version of the web interface, it caches some data, which the new version doesn't understand, so stops. In Chrome, attempt a connection to your printer, then Select Tools > Developer tools (or press F12), open the drop down 'Local Storage', select the IP address of your printer (which should show). You'll see two 'Keys'; 'settings' and 'temps'. Delete 'temps', or both of them. Shut the Chrome window, then try reconnecting. In Firefox, clear the settings by clearing Preferences > Advanced > Network, then clear Cached Web Content. In other browsers, you need to do something similar. Alternatively, changing the printer IP address will also work.
We're in the process of a heavy revision to the networking code, which will be much improved. Our firmware release schedule will be much more frequent than it has been, and issues like this will be corrected.
Generally, I don't think the issues you're experiencing are bugs, more issues with your setup. This 'Issues' part of github is for firmware bugs and feature requests, not for support. For further support, please email support@reprappro.com
Ian
RepRapPro tech support

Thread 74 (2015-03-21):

1.04 no longer possible to heat up extruder

mansj, 2015-03-21:
I'm using Simplify3D, and after firmware update today I can no longer turn on extruder one, and no temperatures are returned to the software. I can turn on the heat pad, but the temp is not reported back.

RRP-support, 2015-03-21:
This is an automated reply to your message "[RepRapFirmware] 1.04 no longer possible to heat up extruder (#74)" sent to support@reprappro.com.

Dear mansj <notifications@github.com>

Thank you for your email. We endeavour to answer all emails within 24 hours. It may take longer during busy times, and holiday periods. We process all customer queries on a first come first served basis, during our office hours which are 9am to 5pm GMT Mon-Fri.

Other support channels are available. Please refer to the relevant troubleshooting guide for your machine:

Ormerod 2: https://reprappro.com/documentation/ormerod-2/troubleshooting/
Ormerod: https://reprappro.com/documentation/ormerod/troubleshooting/

Huxley Duo: https://reprappro.com/documentation/huxley-duo/troubleshooting/
Huxley: https://reprappro.com/documentation/huxley/troubleshooting/

Mono and Tricolour Mendel: https://reprappro.com/documentation/mendel-tricolour/troubleshooting/

Support is also available from other owners of RepRapPro and other 3D printers, either through the RepRap Forums: https://forums.reprap.org or through IRC which can be accessed from here: https://reprappro.com/support-channel/ (works on Chrome, not Firefox).

Best regards,

RepRapPro Support Team.

dc42, 2015-03-21:
RepRapPro renumbered the tools in version 1.04 so that the first extruder is numbered T0, instead of T1 as it as in version 0.78c. So, if you have taken the new config.g file from RRP's 1.04 release then the first extruder will now be T0; and if you have Cura configured to use T1 as the first tool, then the tool numbers in the gcode files it produces will be wrong. If this is the case, you can revert to your old config,.g file, or you can reconfigure Cura and generate new gcode.

You might also wish to look at my 1.04a-dc42 release, see http://forums.reprap.org/read.php?340,486462.

RRP-support, 2015-03-21:
This is an automated reply to your message "Re: [RepRapFirmware] 1.04 no longer possible to heat up extruder
 (#74)" sent to support@reprappro.com.

Dear dc42 <notifications@github.com>

Thank you for your email. We endeavour to answer all emails within 24 hours. It may take longer during busy times, and holiday periods. We process all customer queries on a first come first served basis, during our office hours which are 9am to 5pm GMT Mon-Fri.

Other support channels are available. Please refer to the relevant troubleshooting guide for your machine:

Ormerod 2: https://reprappro.com/documentation/ormerod-2/troubleshooting/
Ormerod: https://reprappro.com/documentation/ormerod/troubleshooting/

Huxley Duo: https://reprappro.com/documentation/huxley-duo/troubleshooting/
Huxley: https://reprappro.com/documentation/huxley/troubleshooting/

Mono and Tricolour Mendel: https://reprappro.com/documentation/mendel-tricolour/troubleshooting/

Support is also available from other owners of RepRapPro and other 3D printers, either through the RepRap Forums: https://forums.reprap.org or through IRC which can be accessed from here: https://reprappro.com/support-channel/ (works on Chrome, not Firefox).

Best regards,

RepRapPro Support Team.

RRP-support, 2015-03-23:
In 1.04, the first hot end is assigned T0, rather than T1. Not an issue for new users, as all our settings and gcode that is supplied have also been updated. Users upgrading from older versions do need to be aware of this, of course, but can still define the hot end as T1 if they want, by editing config.g. Or, if in a single colour machine, define both T0 and T1 to use the same heater and extruder. Using T0 as the first tool has become the industry standard, and is what Repetier and Cura expect out of the box.

dc42 - I appreciate the help, but please don't promote your version of the firmware as an alternative to ours, in this 'Issues' section. That just muddies the waters. Particularly as your firmware, while it currently specifies T1, is going to change to T0, too. Also you've put a hard link into your reply, and if someone with this issue follows it, subsequent releases by you may be overlooked. Also, if the mansj replies to this thread, it may be an issue regarding your version, not ours!

Ian
RepRapPro tech support

mansj, 2015-03-23:
Thank you for the reply. I've got the extruder numbering down - however, the software I'm using (Simplify3D) seems to no longer be able to activate either extruder or monitor any temperature.

I am aware that you can not support Simplify 3D, and indeed my Ormerod 2 is not on the list of supported hardware for Simplify 3D, but it WAS working fine until the new firmware.

RRP-support, 2015-03-23:
This is an automated reply to your message "Re: [RepRapFirmware] 1.04 no longer possible to heat up extruder
 (#74)" sent to support@reprappro.com.

Dear mansj <notifications@github.com>

Thank you for your email. We endeavour to answer all emails within 24 hours. It may take longer during busy times, and holiday periods. We process all customer queries on a first come first served basis, during our office hours which are 9am to 5pm GMT Mon-Fri.

Other support channels are available. Please refer to the relevant troubleshooting guide for your machine:

Ormerod 2: https://reprappro.com/documentation/ormerod-2/troubleshooting/
Ormerod: https://reprappro.com/documentation/ormerod/troubleshooting/

Huxley Duo: https://reprappro.com/documentation/huxley-duo/troubleshooting/
Huxley: https://reprappro.com/documentation/huxley/troubleshooting/

Mono and Tricolour Mendel: https://reprappro.com/documentation/mendel-tricolour/troubleshooting/

Support is also available from other owners of RepRapPro and other 3D printers, either through the RepRap Forums: https://forums.reprap.org or through IRC which can be accessed from here: https://reprappro.com/support-channel/ (works on Chrome, not Firefox).

Best regards,

RepRapPro Support Team.

RRP-support, 2015-03-23:
Hi mansj

I can't think of anything that would specifically stop it working, but I don't have Simplyfy 3D available to test. Check in Pronterface or the web interface that you are getting a correct temperature, and the tool is enabled (ie that it is not reporting a temperature fault). If you want to try setting the hot end back to T1, in your config.g change the last few lines from:
M563 P0 D0 H1 ; Define tool 0
G10 P0 S-273 R-273 ; Set tool 0 operating and standby temperatures

to:
M563 P1 D0 H1 ; Define tool 1
G10 P1 S-273 R-273 ; Set tool 1 operating and standby temperatures

Let me know if that helps.
Ian
RepRapPro tech support

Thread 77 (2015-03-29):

No "OK" reponse from a M105 request stops Octoprint connecting

OricTosh, 2015-03-29:
I'm running an Ormerod 2 with the latest firmware 1.04 and I wish to use octoprint running on a Raspberry Pi as my controller. Octoprint sends a M105 request upon starting a connection but doesn't get the "OK" so wont finish it's connection routine and show machine connected.

I posted about this on the octoprint mailing list
https://groups.google.com/forum/?fromgroups#!topic/octoprint/vCrgYblhOWA
It would great if this was supported by rep-rap firmware

RRP-support, 2015-03-29:
This is an automated reply to your message "[RepRapFirmware] No "OK" reponse from a M105 request stops Octoprint
 connecting (#77)" sent to support@reprappro.com.

Dear Chris Hills <notifications@github.com>

Thank you for your email. We endeavour to answer all emails within 24 hours. It may take longer during busy times, and holiday periods. We process all customer queries on a first come first served basis, during our office hours which are 9am to 5pm GMT Mon-Fri.

Other support channels are available. Please refer to the relevant troubleshooting guide for your machine:

Ormerod 2: https://reprappro.com/documentation/ormerod-2/troubleshooting/
Ormerod: https://reprappro.com/documentation/ormerod/troubleshooting/

Huxley Duo: https://reprappro.com/documentation/huxley-duo/troubleshooting/
Huxley: https://reprappro.com/documentation/huxley/troubleshooting/

Mono and Tricolour Mendel: https://reprappro.com/documentation/mendel-tricolour/troubleshooting/

Support is also available from other owners of RepRapPro and other 3D printers, either through the RepRap Forums: https://forums.reprap.org or through IRC which can be accessed from here: https://reprappro.com/support-channel/ (works on Chrome, not Firefox).

Best regards,

RepRapPro Support Team.

reprappro, 2015-03-31:
We've just checked and it does send ok.  Can you use a direct serial link (for example with Arduino Serial Monitor), send an M105 and paste the response you get?

Best wishes

RepRapPro Support Team

RRP-support, 2015-03-31:
This is an automated reply to your message "Re: [RepRapFirmware] No "OK" reponse from a M105 request stops
 Octoprint connecting (#77)" sent to support@reprappro.com.

Dear reprappro <notifications@github.com>

Thank you for your email. We endeavour to answer all emails within 24 hours. It may take longer during busy times, and holiday periods. We process all customer queries on a first come first served basis, during our office hours which are 9am to 5pm GMT Mon-Fri.

Other support channels are available. Please refer to the relevant troubleshooting guide for your machine:

Ormerod 2: https://reprappro.com/documentation/ormerod-2/troubleshooting/
Ormerod: https://reprappro.com/documentation/ormerod/troubleshooting/

Huxley Duo: https://reprappro.com/documentation/huxley-duo/troubleshooting/
Huxley: https://reprappro.com/documentation/huxley/troubleshooting/

Mono and Tricolour Mendel: https://reprappro.com/documentation/mendel-tricolour/troubleshooting/

Support is also available from other owners of RepRapPro and other 3D printers, either through the RepRap Forums: https://forums.reprap.org or through IRC which can be accessed from here: https://reprappro.com/support-channel/ (works on Chrome, not Firefox).

Best regards,

RepRapPro Support Team.

OricTosh, 2015-04-01:
This was the response I got when I used a direct serial link
ok T:21.6 B: 21.8
Not sure what happening when this received by Octoprint, as it won't connect. Maybe it's the format and content of the string being sent or "what Octoprint is looking for" when it receives the data, that causes the problem. Will update the Octoprint mailing list with my M105 response.

Thanks
Chris

RRP-support, 2015-04-01:
This is an automated reply to your message "Re: [RepRapFirmware] No "OK" reponse from a M105 request stops
 Octoprint connecting (#77)" sent to support@reprappro.com.

Dear Chris Hills <notifications@github.com>

Thank you for your email. We endeavour to answer all emails within 24 hours. It may take longer during busy times, and holiday periods. We process all customer queries on a first come first served basis, during our office hours which are 9am to 5pm GMT Mon-Fri.

Other support channels are available. Please refer to the relevant troubleshooting guide for your machine:

Ormerod 2: https://reprappro.com/documentation/ormerod-2/troubleshooting/
Ormerod: https://reprappro.com/documentation/ormerod/troubleshooting/

Huxley Duo: https://reprappro.com/documentation/huxley-duo/troubleshooting/
Huxley: https://reprappro.com/documentation/huxley/troubleshooting/

Mono and Tricolour Mendel: https://reprappro.com/documentation/mendel-tricolour/troubleshooting/

Support is also available from other owners of RepRapPro and other 3D printers, either through the RepRap Forums: https://forums.reprap.org or through IRC which can be accessed from here: https://reprappro.com/support-channel/ (works on Chrome, not Firefox).

Best regards,

RepRapPro Support Team.

OricTosh, 2015-04-01:
I'm now able to connect to my printer with OctoPrint and rep-rap firmware gives the correct response needed.

tankboyben, 2015-07-09:
What was the solution

RRP-support, 2015-07-09:
This is an automated reply to your message "Re: [RepRapFirmware] No "OK" reponse from a M105 request stops
 Octoprint connecting (#77)" sent to support@reprappro.com.

Dear tankboyben <notifications@github.com>

Thank you for your email. We endeavour to answer all emails within 24 hours. It may take longer during busy times, and holiday periods. We process all customer queries on a first come first served basis, during our office hours which are 9am to 5pm GMT Mon-Fri.

Other support channels are available. Please refer to the relevant troubleshooting guide for your machine:

Ormerod 2: https://reprappro.com/documentation/ormerod-2/troubleshooting/
Ormerod: https://reprappro.com/documentation/ormerod/troubleshooting/

Huxley Duo: https://reprappro.com/documentation/huxley-duo/troubleshooting/
Huxley: https://reprappro.com/documentation/huxley/troubleshooting/

Mono and Tricolour Mendel: https://reprappro.com/documentation/mendel-tricolour/troubleshooting/

Support is also available from other owners of RepRapPro and other 3D printers, either through the RepRap Forums: https://forums.reprap.org or through IRC which can be accessed from here: https://reprappro.com/support-channel/ (works on Chrome, not Firefox).

Best regards,

RepRapPro Support Team.

Closed 2015-04-01.

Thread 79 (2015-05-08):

Does not work with arduino

JelleB, 2015-05-08:
Somewhere along the line of development, the requirement to built the firmware with plain arduino got lost, I think that is a very bad thing.
The board is based on the Arduino due not only because those designs were available, but presumably also because Arduino is a very low threshold entry into programming. That makes it very easy for unskilled enthusiasts to compile and change Arduino programs themselves, but also to contribute those changes back to the community.
I count 11 hurdles to take (some with substeps a) to e)) to built this firmware. In contrast, to compile Marlin, you only have to download the source and click on the .ino.  Now tell me, which firmware is easier to hack, and which one will get the most contributions?
Don't get me wrong, it is very understandable why you'd rather go to eclipse if you are doing this fulltime. There is nothing wrong with that. What is wrong, is that in doing so, apparently support for compiling with Arduino got lost. For any OSS project to succeed, you need mindshare. Arduino is a very successful project, just because of that mindshare. Basing the duet on the due was a very good move. Moving away from arduino for the firmware negates all that.
So, please add a .ino that allows you to compile with arduino?

RRP-support, 2015-05-08:
This is an automated reply to your message "[RepRapFirmware] Does not work with arduino (#79)" sent to support@reprappro.com.

Dear Jelle Boomstra <notifications@github.com>

Thank you for your email. We endeavour to answer all emails within 24 hours. It may take longer during busy times, and holiday periods. We process all customer queries on a first come first served basis, during our office hours which are 9am to 5pm GMT Mon-Fri.

Other support channels are available. Please refer to the relevant troubleshooting guide for your machine:

Ormerod 2: https://reprappro.com/documentation/ormerod-2/troubleshooting/
Ormerod: https://reprappro.com/documentation/ormerod/troubleshooting/

Huxley Duo: https://reprappro.com/documentation/huxley-duo/troubleshooting/
Huxley: https://reprappro.com/documentation/huxley/troubleshooting/

Mono and Tricolour Mendel: https://reprappro.com/documentation/mendel-tricolour/troubleshooting/

Support is also available from other owners of RepRapPro and other 3D printers, either through the RepRap Forums: https://forums.reprap.org or through IRC which can be accessed from here: https://reprappro.com/support-channel/ (works on Chrome, not Firefox).

Best regards,

RepRapPro Support Team.

RRP-support, 2015-05-11:
Hi JelleB
Thanks for the feedback. We are aware this is an issue, and are working to get the firmware compiling again under Arduino IDE. The main problem has been recent changes to the Arduino IDE; it was compiling, but now we need to make further changes to get it working again.
Ian
RepRapPro tech support

chrishamm, 2015-05-11:
The main reason RepRapFirmware does not compile with the stock Arduino IDE lies in its dependency to third-party libraries, which are still way easier to integrate in Eclipse. Please keep in mind that different libraries like LWIP and parts of the ASF, which are not included in the original Arduino package, are needed to get the Ethernet interface working and to utilise other features the rather new SAM8XE 32-bit processor. Marlin OTOH does not have such dependencies, however its functionality and power is very limited compared to RepRapFirmware, which also runs on an entirely differnet architecture (AVR vs. ARM).

Besides, since Arduino v1.5.8 the Arduino Due package had been dropped from the core package and they did not provide a nice way to integrate other Arduino-compatible boards from their Boards Manager. Fortunately they've added a new way to do so to their v1.6.4 release, so I will write a new package file for the Duet over the next few days and update the build instructions once again. I hope this will simplify the build process, and hopefully restore the ability to compile the firmware via the Arduino IDE. I can't guarantee I'll get the latter part working, though, but I'll definitely try.

RRP-support, 2015-05-11:
This is an automated reply to your message "Re: [RepRapFirmware] Does not work with arduino (#79)" sent to support@reprappro.com.

Dear Christian Hammacher <notifications@github.com>

Thank you for your email. We endeavour to answer all emails within 24 hours. It may take longer during busy times, and holiday periods. We process all customer queries on a first come first served basis, during our office hours which are 9am to 5pm GMT Mon-Fri.

Other support channels are available. Please refer to the relevant troubleshooting guide for your machine:

Ormerod 2: https://reprappro.com/documentation/ormerod-2/troubleshooting/
Ormerod: https://reprappro.com/documentation/ormerod/troubleshooting/

Huxley Duo: https://reprappro.com/documentation/huxley-duo/troubleshooting/
Huxley: https://reprappro.com/documentation/huxley/troubleshooting/

Mono and Tricolour Mendel: https://reprappro.com/documentation/mendel-tricolour/troubleshooting/

Support is also available from other owners of RepRapPro and other 3D printers, either through the RepRap Forums: https://forums.reprap.org or through IRC which can be accessed from here: https://reprappro.com/support-channel/ (works on Chrome, not Firefox).

Best regards,

RepRapPro Support Team.

chrishamm, 2015-05-24:
Alright, meanwhile I can say that this would be mission impossible! The reason is that the networking stack (LWIP) has a too complex directory structure for Arduino. It cannot be built with Arduino IDE, although all other libraries can be built just nicely.

Thanks to the changes introduced by Arduino 1.6.4, we can now at least provide the Duet files as an individual boards package (see https://github.com/chrishamm/RepRapFirmware/tree/dev/Hardware). However, a build script is needed to compile the firmware due to the problem I mentioned above. I've updated 3D-ES's Bash script to take care of the required changes (see https://github.com/chrishamm/RepRapFirmware/blob/dev/3d-es-make.sh), however for the moment it cannot be used under Windows, but will work on Linux and most likely on OS X.

I will come up with a more generic approach (some kind of Makefile) in near future, but even then the user will have to install Make on a Windows environment (presuming it isn't already installed by VC++ or so). I wish there was a way to use Arduino IDE to build it entirely, however as I already explained this is (currently) not possible. Sorry!

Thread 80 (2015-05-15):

Webinterface: layer statistics graph

hieronymousch, 2015-05-15:
Hi,

Very much loving the new webinterface (ditched pronterface & repetier).
One small detail: webinterface doesn't update the layer statistics graph as you can see in the screenshot.
Working in FireFox.

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

RRP-support, 2015-05-15:
This is an automated reply to your message "[RepRapFirmware] Webinterface: layer statistics graph (#80)" sent to support@reprappro.com.

Dear hieronymousch <notifications@github.com>

Thank you for your email. We endeavour to answer all emails within 24 hours. It may take longer during busy times, and holiday periods. We process all customer queries on a first come first served basis, during our office hours which are 9am to 5pm GMT Mon-Fri.

Other support channels are available. Please refer to the relevant troubleshooting guide for your machine:

Ormerod 2: https://reprappro.com/documentation/ormerod-2/troubleshooting/
Ormerod: https://reprappro.com/documentation/ormerod/troubleshooting/

Huxley Duo: https://reprappro.com/documentation/huxley-duo/troubleshooting/
Huxley: https://reprappro.com/documentation/huxley/troubleshooting/

Mono and Tricolour Mendel: https://reprappro.com/documentation/mendel-tricolour/troubleshooting/

Support is also available from other owners of RepRapPro and other 3D printers, either through the RepRap Forums: https://forums.reprap.org or through IRC which can be accessed from here: https://reprappro.com/support-channel/ (works on Chrome, not Firefox).

Best regards,

RepRapPro Support Team.

RRP-support, 2015-05-15:
Hi  hieronymousch
How are you generating gcode? Slic3r, Cura or some other gcode editor? Or through Repetier Host?
To get the layer statistics working, the web interface has to find the last Z move in the gcode file, which defines the object height. We've noticed a small bug in the web interface that causes it to ignore the last Z move if it is followed by a 'comment' (a text note preceded by ';'). This can happen if you have verbose Gcode turned on (Slic3r > Print Settings > Output options > Output file > Verbose G-code). This puts a 'comment' (text preceded with';') on every line, so the web interface cannot determine the object height.
Also, files which have been uploaded by USB (eg through Pronterface) have comments removed; the filament usage is held in a comment, so this gets deleted. The web interface will report just file usage and layer time statistics, then.
If you can post a portion of your gcode, or email it to me at support@reprappro.com , I'll take a look and see if it's anything else that may be causing it.
Ian
RepRapPro tech support

hieronymousch, 2015-05-15:
Hi,

Thanks for your quick reply. I indeed used slic3r (version 1.26) but not with the verbode G-code optiion. I do however get some comments on the end of the G-code file.
I mailed a small gcode file to support email.

Thanks,

J

RRP-support, 2015-05-15:
This is an automated reply to your message "Re: [RepRapFirmware] Webinterface: layer statistics graph (#80)" sent to support@reprappro.com.

Dear hieronymousch <notifications@github.com>

Thank you for your email. We endeavour to answer all emails within 24 hours. It may take longer during busy times, and holiday periods. We process all customer queries on a first come first served basis, during our office hours which are 9am to 5pm GMT Mon-Fri.

Other support channels are available. Please refer to the relevant troubleshooting guide for your machine:

Ormerod 2: https://reprappro.com/documentation/ormerod-2/troubleshooting/
Ormerod: https://reprappro.com/documentation/ormerod/troubleshooting/

Huxley Duo: https://reprappro.com/documentation/huxley-duo/troubleshooting/
Huxley: https://reprappro.com/documentation/huxley/troubleshooting/

Mono and Tricolour Mendel: https://reprappro.com/documentation/mendel-tricolour/troubleshooting/

Support is also available from other owners of RepRapPro and other 3D printers, either through the RepRap Forums: https://forums.reprap.org or through IRC which can be accessed from here: https://reprappro.com/support-channel/ (works on Chrome, not Firefox).

Best regards,

RepRapPro Support Team.

RRP-support, 2015-05-27:
Hi hieronymousch
I have replied by email, but I think the problem is you are using 'Lift Z'; ie between each move, the Z moves up, moves in X and Y, then down again, and does the same thing at the end of each layer. This is set in Slic3r > Printer Settings > Extruder 1 > Retraction > Lift Z. We normally have this set to 0. I'd guess having this set messes up the layer statistics! I get the same thing as you when I print this gcode. I've sent it to our programmer, and we'll have a look at whether we can do anything about this. I'll let you know what our programmer says.
Ian
RepRapPro tech support

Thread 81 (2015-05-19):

what's the g-code for color?

columbus1231, 2015-05-19:
I am wondering how color is represented in g-code after conversion from an amf file.
For example, just like a straight linear movement is represented in g-code as G1 Xnnn Ynnn Znnn Ennn Fnnn Snnn. How is the red green blue (rgb) color code read in g-code by a 3d printer in a section?

RRP-support, 2015-05-19:
This is an automated reply to your message "[RepRapFirmware] what's the g-code for color? (#81)" sent to support@reprappro.com.

Dear columbus1231 <notifications@github.com>

Thank you for your email. We endeavour to answer all emails within 24 hours. It may take longer during busy times, and holiday periods. We process all customer queries on a first come first served basis, during our office hours which are 9am to 5pm GMT Mon-Fri.

Other support channels are available. Please refer to the relevant troubleshooting guide for your machine:

Ormerod 2: https://reprappro.com/documentation/ormerod-2/troubleshooting/
Ormerod: https://reprappro.com/documentation/ormerod/troubleshooting/

Huxley Duo: https://reprappro.com/documentation/huxley-duo/troubleshooting/
Huxley: https://reprappro.com/documentation/huxley/troubleshooting/

Mono and Tricolour Mendel: https://reprappro.com/documentation/mendel-tricolour/troubleshooting/

Support is also available from other owners of RepRapPro and other 3D printers, either through the RepRap Forums: https://forums.reprap.org or through IRC which can be accessed from here: https://reprappro.com/support-channel/ (works on Chrome, not Firefox).

Best regards,

RepRapPro Support Team.

RRP-support, 2015-05-19:
Colour is not represented in the gcode file at all... yet. This is mainly because the standard .stl file type does not support colour. All the gcode file can do is change tools, for different stl parts. It is up to you to put the correct colour for the specific part of the print in the right tool (ie, different hot end). Then the gcode changes tool, to use a different extruder/hot end.
If mixing hot ends, ie a single nozzle fed by multiple extruders, become common place, there will have to eventually be some mechanism for this. Our firmware does at least allow you to set up any number of tools, with any mix of extruders (different tools can use different combinations of the same extruder), feeding a single hot end. I'm not sure if you can specify tools with different percentages for extruders (ie rather than 50% extruder 1, 50% extruder 2, you mix 20% and 80%, to get a wider variation of colour), but that is anticipated. You can also manually change the gcode to set different extruder motor speeds, to get different colours, and graduated mixes of colours, but there's no native file format or slicing program that can do this.
In the end, the hardware is there, and it's a software problem. How do you create blended colour in a CAD file, what format do you output to, and how do you slice that object to represent the colour and/or material you want, for the printer firmware to understand?! Tricky problems to resolve!

Ian
RepRapPro tech support

RRP-support, 2015-05-19:
Also, you wouldn't mix Red, green and blue; this is a transmissive colour palette. You would mix White, Cyan, Magenta, Yellow and Black, which is a reflective colour palette (like paper printer print) to get a wide range of colours for 3D objects.

Ian
RepRapPro tech support

columbus1231, 2015-05-20:
Thanks for your help. I will try your suggestion and see on my printer.

RRP-support, 2015-05-20:
This is an automated reply to your message "Re: [RepRapFirmware] what's the g-code for color? (#81)" sent to support@reprappro.com.

Dear columbus1231 <notifications@github.com>

Thank you for your email. We endeavour to answer all emails within 24 hours. It may take longer during busy times, and holiday periods. We process all customer queries on a first come first served basis, during our office hours which are 9am to 5pm GMT Mon-Fri.

Other support channels are available. Please refer to the relevant troubleshooting guide for your machine:

Ormerod 2: https://reprappro.com/documentation/ormerod-2/troubleshooting/
Ormerod: https://reprappro.com/documentation/ormerod/troubleshooting/

Huxley Duo: https://reprappro.com/documentation/huxley-duo/troubleshooting/
Huxley: https://reprappro.com/documentation/huxley/troubleshooting/

Mono and Tricolour Mendel: https://reprappro.com/documentation/mendel-tricolour/troubleshooting/

Support is also available from other owners of RepRapPro and other 3D printers, either through the RepRap Forums: https://forums.reprap.org or through IRC which can be accessed from here: https://reprappro.com/support-channel/ (works on Chrome, not Firefox).

Best regards,

RepRapPro Support Team.

Closed 2015-05-20.

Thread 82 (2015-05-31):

File upload sometimes fails

jasontrublu, 2015-05-31:
Hi,

Firmware Version: 	1.09 (2015-04-21)
Web Interface Version: 	HTML: 1.06, JS: 1.06

Sometimes file uploads fail / get stuck. It loads until about 98/99% and then just freezes (without aborting or reporting anything). It seems to happen more often to big files, but bigger files can be successful as well.

RRP-support, 2015-05-31:
This is an automated reply to your message "[RepRapFirmware] File upload sometimes fails (#82)" sent to support@reprappro.com.

Dear Jason Peper <notifications@github.com>

Thank you for your email. We endeavour to answer all emails within 24 hours. It may take longer during busy times, and holiday periods. We process all customer queries on a first come first served basis, during our office hours which are 9am to 5pm GMT Mon-Fri.

Other support channels are available. Please refer to the relevant troubleshooting guide for your machine:

Ormerod 2: https://reprappro.com/documentation/ormerod-2/troubleshooting/
Ormerod: https://reprappro.com/documentation/ormerod/troubleshooting/

Huxley Duo: https://reprappro.com/documentation/huxley-duo/troubleshooting/
Huxley: https://reprappro.com/documentation/huxley/troubleshooting/

Mono and Tricolour Mendel: https://reprappro.com/documentation/mendel-tricolour/troubleshooting/

Support is also available from other owners of RepRapPro and other 3D printers, either through the RepRap Forums: https://forums.reprap.org or through IRC which can be accessed from here: https://reprappro.com/support-channel/ (works on Chrome, not Firefox).

Best regards,

RepRapPro Support Team.

chrishamm, 2015-06-03:
How big is the file you were trying to upload? I recently uploaded a file that was 20MB big and it worked just well on my machine. Also, which OS and browser are you using?

RRP-support, 2015-06-03:
This is an automated reply to your message "Re: [RepRapFirmware] File upload sometimes fails (#82)" sent to support@reprappro.com.

Dear Christian Hammacher <notifications@github.com>

Thank you for your email. We endeavour to answer all emails within 24 hours. It may take longer during busy times, and holiday periods. We process all customer queries on a first come first served basis, during our office hours which are 9am to 5pm GMT Mon-Fri.

Other support channels are available. Please refer to the relevant troubleshooting guide for your machine:

Ormerod 2: https://reprappro.com/documentation/ormerod-2/troubleshooting/
Ormerod: https://reprappro.com/documentation/ormerod/troubleshooting/

Huxley Duo: https://reprappro.com/documentation/huxley-duo/troubleshooting/
Huxley: https://reprappro.com/documentation/huxley/troubleshooting/

Mono and Tricolour Mendel: https://reprappro.com/documentation/mendel-tricolour/troubleshooting/

Support is also available from other owners of RepRapPro and other 3D printers, either through the RepRap Forums: https://forums.reprap.org or through IRC which can be accessed from here: https://reprappro.com/support-channel/ (works on Chrome, not Firefox).

Best regards,

RepRapPro Support Team.

RRP-support, 2015-06-03:
Hi jasontrublu

We also don't have any problems with big file uploads; v1.09 is much more stable than older versions when it comes to the web interface. A couple of things to check: first, check that you are using the correct SD-Image; if you're using SD files that were meant for an older version of the firmware, they may not work correctly with the current version. ALWAYS use the SD Image supplied with the firmware. If you're using firmware 1.09, the web interface should look like this: https://reprappro.com/wp-content/uploads/2015/04/web-interface-1024x576.png

It could also be a corrupt SD card, particularly if you have had a failed or interrupted file upload. Check the SD card on your PC (use chkdsk) and/or reformat the SD card (copy off any files you have changed first, eg config.g). I find the official SD formatting tool to be the best to reformat the SD cards: https://www.sdcard.org/downloads/formatter_4/index.html

Ian
RepRapPro tech support

jasontrublu, 2015-07-04:
I have not yet have time to investigate this again, as I was on vacation in the UK :)

But the problem is not size alone. I have uploaded bigger files as well. I will write if I had time to investigate further

RRP-support, 2015-07-04:
This is an automated reply to your message "Re: [RepRapFirmware] File upload sometimes fails (#82)" sent to support@reprappro.com.

Dear Jason Peper <notifications@github.com>

Thank you for your email. We endeavour to answer all emails within 24 hours. It may take longer during busy times, and holiday periods. We process all customer queries on a first come first served basis, during our office hours which are 9am to 5pm GMT Mon-Fri.

Other support channels are available. Please refer to the relevant troubleshooting guide for your machine:

Ormerod 2: https://reprappro.com/documentation/ormerod-2/troubleshooting/
Ormerod: https://reprappro.com/documentation/ormerod/troubleshooting/

Huxley Duo: https://reprappro.com/documentation/huxley-duo/troubleshooting/
Huxley: https://reprappro.com/documentation/huxley/troubleshooting/

Mono and Tricolour Mendel: https://reprappro.com/documentation/mendel-tricolour/troubleshooting/

Support is also available from other owners of RepRapPro and other 3D printers, either through the RepRap Forums: https://forums.reprap.org or through IRC which can be accessed from here: https://reprappro.com/support-channel/ (works on Chrome, not Firefox).

Best regards,

RepRapPro Support Team.

Moosball, 2015-07-19:
I have the same Problem, im on 1.09 Firmware, using Firefox 39.0. I have formated with the sdcard formatter but no change.
It seems when i upload & print, it works most of the time. but when i just upload, it gets stuck at between 97 and 99 percent. (it was the same gcode file, size 1,3MB).

Regards

RRP-support, 2015-07-19:
This is an automated reply to your message "Re: [RepRapFirmware] File upload sometimes fails (#82)" sent to support@reprappro.com.

Dear Moosball <notifications@github.com>

Thank you for your email. We endeavour to answer all emails within 24 hours. It may take longer during busy times, and holiday periods. We process all customer queries on a first come first served basis, during our office hours which are 9am to 5pm GMT Mon-Fri.

Other support channels are available. Please refer to the relevant troubleshooting guide for your machine:

Ormerod 2: https://reprappro.com/documentation/ormerod-2/troubleshooting/
Ormerod: https://reprappro.com/documentation/ormerod/troubleshooting/

Huxley Duo: https://reprappro.com/documentation/huxley-duo/troubleshooting/
Huxley: https://reprappro.com/documentation/huxley/troubleshooting/

Mono and Tricolour Mendel: https://reprappro.com/documentation/mendel-tricolour/troubleshooting/

Support is also available from other owners of RepRapPro and other 3D printers, either through the RepRap Forums: https://forums.reprap.org or through IRC which can be accessed from here: https://reprappro.com/support-channel/ (works on Chrome, not Firefox).

Best regards,

RepRapPro Support Team.
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
Moosball, 2015-08-30:
Hello Chrishamm,

Sorry again for the delay, holidays called :)
Well, i had time now and replaced the class 4 Card i got from reprappro. now i have a 16gb class 10 Card insert and made some upload test, one by one, many by one, and it seems to work all the time.
i tryed to Format the class 4 Card, and had no Problem. maybe it has something to do with the transerferspeed through Ethernet.

atm this part works :) lets see if i can find a solution for my calibration Problem :) cant print circles (but i go to the guide befor i ask something new.

have a god time, and thanks to all for the help

regards,
Steven

RRP-support, 2015-08-30:
This is an automated reply to your message "Re: [RepRapFirmware] File upload sometimes fails (#82)" sent to support@reprappro.com.

Dear Moosball <notifications@github.com>

Thank you for your email. We endeavour to answer all emails within 24 hours. It may take longer during busy times, and holiday periods. We process all customer queries on a first come first served basis, during our office hours which are 9am to 5pm GMT Mon-Fri.

Other support channels are available. Please refer to the relevant troubleshooting guide for your machine:

Ormerod 2: https://reprappro.com/documentation/ormerod-2/troubleshooting/
Ormerod: https://reprappro.com/documentation/ormerod/troubleshooting/

Huxley Duo: https://reprappro.com/documentation/huxley-duo/troubleshooting/
Huxley: https://reprappro.com/documentation/huxley/troubleshooting/

Mono and Tricolour Mendel: https://reprappro.com/documentation/mendel-tricolour/troubleshooting/

Support is also available from other owners of RepRapPro and other 3D printers, either through the RepRap Forums: https://forums.reprap.org or through IRC which can be accessed from here: https://reprappro.com/support-channel/ (works on Chrome, not Firefox).

Best regards,

RepRapPro Support Team.

Moosball, 2015-09-10:
Hello Chrishamm,

Well, now i have the same problem again. I dont know what to do. Change my network cable, network switch, and noting works. yesterday i tryed e 13mb file, today its 1,1mb file. I just stops at close to the end of upload.

Maybe you have a chance to build me a firmware with some debug ?

kind regards,
Steven

RRP-support, 2015-09-10:
Copy your 'sys' folder from the SD card to your PC. Reformat the SD card. Copy the SD Image to the card. Copy your old 'sys' folder to the SD card.
Most likely there is a corrupt file that the firmware can't cope with.
Ian
RepRapPro tech support

Moosball, 2015-09-21:
Hi there,
Thanks for you help, but i couldnt reslove it. i get the error on every file that seems to be larger then 1mb. sometimes, after 3 retry it worked, but most i get the error then earlier then 95-99%. then the error comes at 5-8% and i have to poweroff the duet.

any other ideas ?

reagards,
steven

RRP-support, 2015-09-22:
Hi Steven
It really sounds like a physical problem with the SD card or SD socket, and most likely not related to firmware - we just don't see these sorts of problems caused by the firmware. My best guess is that you need to clean the contacts on the SD socket, as there's a poor connection somewhere.
If you have an aerosol can of Isopropyl Alcohol, disconnect everything from the Duet, and squirt this into the SD card socket, then repeatedly insert and eject the SD card. Wait for the Isopropyl Alcohol to evaporate before reconnecting the Duet. This should clean the contacts.
Also check the soldering of the SD card socket, and check there is nothing bridging the contacts either on the back of the SD card, or pins on the main ARM chip.
Ian
RepRapPro tech support

Moosball, 2015-09-23:
Hello Ian,
I will give it a try, but i dont think it has something to do with the contacts. Like chrishamm mentioned befor when i send the wireshark log, he sayed he misses the final JSON response.

I also changed the SD Card (Class 10), reformated everything.... and it seemed to be fixed, but then the problem came again.

what i want to do today, maybe i can upload the files over the usb connection from pronterface, and see if i have the same errors, so i can see if i have a problem with my homenetwork.

Regards,
Steven

Chrishamm wrote:
Hello Moosball,

No problem, thank you for posting those dumps! I've just looked through them and the problem seems to be that the firmware doesn't send the final JSON response when the upload has finished. The transmission itself looks good to me (I can't tell much about the last 22% dump though), but the question remains why the firmware cannot save/close the file. For this reason I'd like to ask you to perform the following steps..

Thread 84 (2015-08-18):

_Calibration-200x200.g Print Fails On Start(Heaters Turn Off)

trybry25, 2015-08-18:
Hi, I'm wondering if anyone can help me with getting my printer to print the 200x200 calibration build. I have already gon through homing X,Y-axises and zeroing Z-axis as,well as bed-plane leveling. I have also gotten my extruder to extrude alittle using the web interface and some G-codes.
MY PROBLEM IS: when I go to print ._Calibration-200x200.g(or any file) in the web interface, my bed heater and hot-end heater both turn off and nothing happens.
Is there something wrong with the print file? or maybe my config.g? I can't find how to edit the ._Calibration-200x200.g. Can some one tell me where this file is located? or if there exists a newer file i should be using instead?

Thanks,
Tryg

RRP-support, 2015-08-18:
This is an automated reply to your message "[RepRapFirmware] _Calibration-200x200.g Print Fails On Start(Heaters
 Turn Off) (#84)" sent to support@reprappro.com.

Dear trybry25 <notifications@github.com>

Thank you for your email. We endeavour to answer all emails within 24 hours. It may take longer during busy times, and holiday periods. We process all customer queries on a first come first served basis, during our office hours which are 9am to 5pm GMT Mon-Fri.

Other support channels are available. Please refer to the relevant troubleshooting guide for your machine:

Ormerod 2: https://reprappro.com/documentation/ormerod-2/troubleshooting/
Ormerod: https://reprappro.com/documentation/ormerod/troubleshooting/

Huxley Duo: https://reprappro.com/documentation/huxley-duo/troubleshooting/
Huxley: https://reprappro.com/documentation/huxley/troubleshooting/

Mono and Tricolour Mendel: https://reprappro.com/documentation/mendel-tricolour/troubleshooting/

Support is also available from other owners of RepRapPro and other 3D printers, either through the RepRap Forums: https://forums.reprap.org or through IRC which can be accessed from here: https://reprappro.com/support-channel/ (works on Chrome, not Firefox).

Best regards,

RepRapPro Support Team.

RRP-support, 2015-08-18:
Hi Tryg
This isn't a firmware issue, it's a settings problem. Most likely either your hot end 'tool' is not set to T0 that the gcode asks for, or there is some other issue. Please email support@reprappro.com with your problem, what printer you have, and any other relevant setup information. Also please send your config.g file, and tell me what firmware version you are using (send M115 to the printer). Make sure you print the 'Calibration-200x200.g' file, not one named with an '_' at the beginning; these are temporary files, not print files.
Ian
RepRapPro tech support

trybry25, 2015-08-18:
Oh, I seam to have been trying the wrong file. That fixed my problem, although, I'm still having some issues: The calibration peice starts before the hot end is actually hot enough, causing the E-motor to click abit before it actually start extruding. Also, whenever i try to heat bed and hotend simultaniously from room temperature, it overloads my UPS. Is it necessary for the hot end to draw so much power will heating upto standby?
I am using version 1.09 It looks like there is a new version available, I'll check that out and see if it helps

Thanks Again,

RRP-support, 2015-08-18:
This is an automated reply to your message "Re: [RepRapFirmware] _Calibration-200x200.g Print Fails On
 Start(Heaters Turn Off) (#84)" sent to support@reprappro.com.

Dear trybry25 <notifications@github.com>

Thank you for your email. We endeavour to answer all emails within 24 hours. It may take longer during busy times, and holiday periods. We process all customer queries on a first come first served basis, during our office hours which are 9am to 5pm GMT Mon-Fri.

Other support channels are available. Please refer to the relevant troubleshooting guide for your machine:

Ormerod 2: https://reprappro.com/documentation/ormerod-2/troubleshooting/
Ormerod: https://reprappro.com/documentation/ormerod/troubleshooting/

Huxley Duo: https://reprappro.com/documentation/huxley-duo/troubleshooting/
Huxley: https://reprappro.com/documentation/huxley/troubleshooting/

Mono and Tricolour Mendel: https://reprappro.com/documentation/mendel-tricolour/troubleshooting/

Support is also available from other owners of RepRapPro and other 3D printers, either through the RepRap Forums: https://forums.reprap.org or through IRC which can be accessed from here: https://reprappro.com/support-channel/ (works on Chrome, not Firefox).

Best regards,

RepRapPro Support Team.

trybry25, 2015-08-18:
and here is my config.g:
; Configuration file for RepRap Mendel 3
; RepRapPro Ltd
;
; Copy this file to config.g if you have a Mendel 3
; If you are updating a config.g that you already have you
; may wish to go through it and this file checking what you
; want to keep from your old file.
;
; For G-code definitions, see http://reprap.org/wiki/G-code
;
M111 S0                             ; Debug off
M550 PRepRapPro Mendel 3            ; Machine name (can be anything you like). With DHCP enabled connect to (example) http://reprappromendel3 (machine name with no spaces).
M551 Preprap                        ; Machine password (currently not used)
M540 P0xBE:0xEF:0xDE:0xAD:0xFE:0x14 ; MAC Address
;M552 P0.0.0.0                       ; Un-comment for DHCP
M552  P172.16.138.125   ;P192.168.1.14                  ; IP address, comment for DHCP
M553  P255.255.255.0    ;P255.255.255.0                 ; Netmask
M554  P172.16.138.1     ;P192.168.1.1                   ; Gateway, comment for DHCP
M555 P2                             ; Set output to look like Marlin
G21                                 ; Work in millimetres
G90                                 ; Send absolute corrdinates...
M83                                 ; ...but relative extruder moves
M906 X800 Y1000 Z800 E800           ; Set motor currents (mA)
M305 P0 R4700                       ; Set the heated bed thermistor series resistor to 4K7
M305 P1 R4700                       ; Set the hot end thermistor series resistor to 4K7
M569 P0 S1                          ; Reverse the X motor
M569 P3 S0                          ; Reverse the extruder motor (T0)
M569 P4 S0                          ; Reverse the extruder motor (T1)
M569 P5 S0                          ; Reverse the extruder motor (T2)
M92 E660                            ; Set extruder steps per mm
M558 P2                             ; Use a modulated Z probe
G31 Z1.5 P543   ;Z0.8 P600             ; Set the probe height and threshold (deliberately too high to avoid bed crashes on initial setup)
M556 S75 X0 Y0 Z0                   ; Put your axis compensation here
M201 X500 Y500 Z15 E500             ; Accelerations (mm/s^2)
M203 X15000 Y15000 Z100 E3600       ; Maximum speeds (mm/min)
M566 X200 Y200 Z30 E20              ; Minimum speeds mm/minute
M563 P0 D0 H1                       ; Define tool 0
G10 P0 S-273 R-273                  ; Set tool 0 operating and standby temperatures
;M563 P1 D1 H2                       ; Define tool 1, uncomment if you have a dual colour upgrade
;G10 P1 S-273 R-273                  ; Set tool 1 operating and standby temperatures, uncomment if you have a dual colour upgrade
;M563 P2 D2 H3                       ; Define tool 2, uncomment if you have a tri colour upgrade
;G10 P2 S-273 R-273                  ; Set tool 2 operating and standby temperatures, uncomment if you have a dual colour upgrade

trybry25, 2015-08-18:
again, M115: FIRMWARE_NAME:RepRapFirmware FIRMWARE_VERSION:1.09 ELECTRONICS:Duet (+ Extension) DATE:2015-04-21

it looks like the recent update is also version 1.09. What is the difference from what i am using?

trybry25, 2015-08-18:
I think my extrusion problem was with my Z-probe settings, and not the heater.. Looks like this thread can be closed...

Thanks again

RRP-support, 2015-08-19:
Hi trybry25
Great, glad you got going. The current firmware is v1.09; there may have been an update to the Readme or some other minor file changes to the SD image, but not to the firmware.
It sounds like you were starting the print too low, blocking the nozzle with the bed, but I think you have sorted that out now, too.
If you have any more support-type questions, please email us on support@reprappro.com - the 'Issues' part of github is more for actual firmware-related issues.
Ian
RepRapPro tech support

Closed 2015-08-18.

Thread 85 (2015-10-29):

Home All does not use proper X,Y coordinates to perform Proximitysensing

gratefulfrog, 2015-10-29:
I have discovered that although the sequence HomeX, HomeY, HomeZ works as expected, a call to Home All, does not work the same way.

In particular, my G31 settings in the config.g file are respected by homez.g but not by homeall.g.

The issue is that homeall causes the head moves too far to the right pushing the proximity sensor beyond the white tape, causing the head to crash into the bed, catastrophically.

The workaround is to never use home all!

I would attach my config.g, homex.g homey.g, homez.g and homeall.g files, but I do not have permission. Contact me if needed.
Cheers,
Bob

RRP-support, 2015-10-29:
This is an automated reply to your message "[RepRapFirmware] Home All does not use proper X,Y coordinates to
 perform Proximitysensing (#85)" sent to support@reprappro.com.

Dear gratefulfrog <notifications@github.com>

Thank you for your email. We endeavour to answer all emails within 24 hours. It may take longer during busy times, and holiday periods. We process all customer queries on a first come first served basis, during our office hours which are 9am to 5pm GMT Mon-Fri.

Other support channels are available. Please refer to the relevant troubleshooting guide for your machine:

Ormerod 2: https://reprappro.com/documentation/ormerod-2/troubleshooting/
Ormerod: https://reprappro.com/documentation/ormerod/troubleshooting/

Huxley Duo: https://reprappro.com/documentation/huxley-duo/troubleshooting/
Huxley: https://reprappro.com/documentation/huxley/troubleshooting/

Mono and Tricolour Mendel: https://reprappro.com/documentation/mendel-tricolour/troubleshooting/

Support is also available from other owners of RepRapPro and other 3D printers, either through the RepRap Forums: https://forums.reprap.org or through IRC which can be accessed from here: https://reprappro.com/support-channel/ (works on Chrome, not Firefox).

Best regards,

RepRapPro Support Team.

gratefulfrog, 2015-10-30:
Here is some updated information, I amnot sure where the problem lies, but I am now pretty sure that there is a problem!

I have determined that during the Home Y process, the X axis point displays are shifted by 4.36mm, but represent the same physical point!

In other words, after homing X, I move the head to X=40, according to the web interface, then measure its physical position relative to a fixed point on the x-axis smooth bars. Say this is 35mm.

Then I home Y, and according to the web interface, we are now at x=44.37, but the physical measurement still shows 35mm from the fixed point.

If I repeat the Y homing, the same point moves another 4.36mm higher on the x display!

Here are the details, all of this was run on a freshly started Huxley Duo:

1. Restart machine completely!
2. Home X:  Head Position: (0.00, 0.00, 0.00)
3. Move to X=40,  (4x X+10) Head Position: (**40.01**, 0.00, 0.00)
4. measure from fixed point on X axis: **35mm**
5. G91: no movement,no changes
6. G1 Z5 F200: head moves up, Head Position: (40.01, 0.00, 5.00)
7. G1 X20 F2000, head moves right, Head Position: (**60.01**, 0.00, 5.00)
8. measure from fixed point on X axis: **15mm <- this seems correct!**
9. G90: no movement, no changes
10. G1 Y-140 F2000 S1: no movement, but Head Position: (**62.19**, 200.06, 5.00) **<- x position +2.18mm?**
11. G92 Y0: no movement, but Head Position: (**62.19**, 0.00, 5.00)
12. G1 Y3 F200: bed moves forward, Head Position: (**62.19**, 3.00, 5.00)
13. G1 Y-5 F200 S1:bed moves backwards, Head Position: (**64.37**, 200.06, 5.00)  **<- x position + another 2.18mm?**
14. G92 Y0: no movement, but Head Position: (**64.37**, 0.00, 5.00)
15. G1 Y0 F2000: no movement, no changes
16. measure from fixed point on X axis: 15mm <- this seems correct, still!
17. G92 Y0: no movement, no changes
18. G91: no movement, no changes
19. G1 X-20 F2000: head moves left: Head Position: (**44.37**, 0.00, 5.00)
20. measure from fixed point on X axis: **35mm**
21. **step 18&19 values are incoherent with values in steps 2&3!!**

RRP-support, 2015-10-30:
This is an automated reply to your message "Re: [RepRapFirmware] Home All does not use proper X,Y coordinates to
 perform Proximitysensing (#85)" sent to support@reprappro.com.

Dear gratefulfrog <notifications@github.com>

Thank you for your email. We endeavour to answer all emails within 24 hours. It may take longer during busy times, and holiday periods. We process all customer queries on a first come first served basis, during our office hours which are 9am to 5pm GMT Mon-Fri.

Other support channels are available. Please refer to the relevant troubleshooting guide for your machine:

Ormerod 2: https://reprappro.com/documentation/ormerod-2/troubleshooting/
Ormerod: https://reprappro.com/documentation/ormerod/troubleshooting/

Huxley Duo: https://reprappro.com/documentation/huxley-duo/troubleshooting/
Huxley: https://reprappro.com/documentation/huxley/troubleshooting/

Mono and Tricolour Mendel: https://reprappro.com/documentation/mendel-tricolour/troubleshooting/

Support is also available from other owners of RepRapPro and other 3D printers, either through the RepRap Forums: https://forums.reprap.org or through IRC which can be accessed from here: https://reprappro.com/support-channel/ (works on Chrome, not Firefox).

Best regards,

RepRapPro Support Team.

dc42, 2015-10-30:
The shifting of X=0 after Y homing, and more particularly after Z homing, is a bug that occurs when axis compensation is enabled. I fixed it in my fork of RepRapFirmware over a year ago. To be honest, I thought it was fixed in the official 1.09 release too.

RRP-support, 2015-10-30:
This is an automated reply to your message "Re: [RepRapFirmware] Home All does not use proper X,Y coordinates to
 perform Proximitysensing (#85)" sent to support@reprappro.com.

Dear dc42 <notifications@github.com>

Thank you for your email. We endeavour to answer all emails within 24 hours. It may take longer during busy times, and holiday periods. We process all customer queries on a first come first served basis, during our office hours which are 9am to 5pm GMT Mon-Fri.

Other support channels are available. Please refer to the relevant troubleshooting guide for your machine:

Ormerod 2: https://reprappro.com/documentation/ormerod-2/troubleshooting/
Ormerod: https://reprappro.com/documentation/ormerod/troubleshooting/

Huxley Duo: https://reprappro.com/documentation/huxley-duo/troubleshooting/
Huxley: https://reprappro.com/documentation/huxley/troubleshooting/

Mono and Tricolour Mendel: https://reprappro.com/documentation/mendel-tricolour/troubleshooting/

Support is also available from other owners of RepRapPro and other 3D printers, either through the RepRap Forums: https://forums.reprap.org or through IRC which can be accessed from here: https://reprappro.com/support-channel/ (works on Chrome, not Firefox).

Best regards,

RepRapPro Support Team.

RRP-support, 2015-10-30:
I've had two reports of problems with firmware v1.09c and orthogonal compensation now. I, too, thought that we had the same compensation in now as yours, dc42. It's possible that the numbers are causing an odd effect. The two settings are:
M556 S49.5 X-0.54 Y-0.54 Z0 (from gratefulfrog)
M556 S80 X-0.35 Y-1.25 Z-0.35 (from Stefan)
Is it possible that the compensation bug was fixed for positive numbers, but not negative? And it's always the Y axis that seems to cause the problem!
Ian
RepRapPro tech support

gratefulfrog, 2015-10-30:
I have run the same test without orthogonal compensation and the problem does not occur!

1. M556 S100 X0 Y0 Z0
2. home X,
3. move X+10 4x
4. displayed X=40.01   measured x distance from fixed point D= 67.5
5. home y
6. displayed X=40.01   measured x distance from fixed point D= 67.5

It would seem to be the orthogonal compensation which is broken.

Stefan3, 2015-11-02:
I figured only the X value in the M556 command affects this behaviour, but it doesn't matter whether it is positive or negative. With positive values for X, the reported X position decreases during homing of Y, with negative numbers it increases. When I keep X at 0 in the M556 command, it seems I can set Y and Z to any value without affecting the reported X position.

RRP-support, 2015-11-02:
This is an automated reply to your message "Re: [RepRapFirmware] Home All does not use proper X,Y coordinates to
 perform Proximitysensing (#85)" sent to support@reprappro.com.

Dear Stefan3 <notifications@github.com>

Thank you for your email. We endeavour to answer all emails within 24 hours. It may take longer during busy times, and holiday periods. We process all customer queries on a first come first served basis, during our office hours which are 9am to 5pm GMT Mon-Fri.

Other support channels are available. Please refer to the relevant troubleshooting guide for your machine:

Ormerod 2: https://reprappro.com/documentation/ormerod-2/troubleshooting/
Ormerod: https://reprappro.com/documentation/ormerod/troubleshooting/

Huxley Duo: https://reprappro.com/documentation/huxley-duo/troubleshooting/
Huxley: https://reprappro.com/documentation/huxley/troubleshooting/

Mono and Tricolour Mendel: https://reprappro.com/documentation/mendel-tricolour/troubleshooting/

Support is also available from other owners of RepRapPro and other 3D printers, either through the RepRap Forums: https://forums.reprap.org or through IRC which can be accessed from here: https://reprappro.com/support-channel/ (works on Chrome, not Firefox).

Best regards,

RepRapPro Support Team.

dc42, 2015-11-02:
The X parameter defines the coupling between X and Y so that makes sense. The other two parameters will probably affect whether X and Z homing cause shifts in the other axes.

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

--
Sent from my Android phone with K-9 Mail. Please excuse my brevity.

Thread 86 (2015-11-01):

M208 fails to set maximum Z movement

gratefulfrog, 2015-11-01:
I am sorry to have to report another issue firmware 1.09,

I would like to set maximum X,Y,Z values to prevent the motors from skipping and/or the head form banging.  However, for the Z axis, the M208 gcode fails to work.

When I run the gcode at the console:
> M208 X131 Y140 Z73

Then I try to manually move the head:
* beyond X=131, the head stops at X=131, and will go no further,
* beyond Y=140, the bed stops at Y=140, and will go no further
* beyond Z=73, **the head continues to climb, with no limit!**

I hope this is not to hard to fix.

Cheers,
Bob

RRP-support, 2015-11-01:
This is an automated reply to your message "[RepRapFirmware] M208 fails to set maximum Z movement (#86)" sent to support@reprappro.com.

Dear gratefulfrog <notifications@github.com>

Thank you for your email. We endeavour to answer all emails within 24 hours. It may take longer during busy times, and holiday periods. We process all customer queries on a first come first served basis, during our office hours which are 9am to 5pm GMT Mon-Fri.

Other support channels are available. Please refer to the relevant troubleshooting guide for your machine:

Ormerod 2: https://reprappro.com/documentation/ormerod-2/troubleshooting/
Ormerod: https://reprappro.com/documentation/ormerod/troubleshooting/

Huxley Duo: https://reprappro.com/documentation/huxley-duo/troubleshooting/
Huxley: https://reprappro.com/documentation/huxley/troubleshooting/

Mono and Tricolour Mendel: https://reprappro.com/documentation/mendel-tricolour/troubleshooting/

Support is also available from other owners of RepRapPro and other 3D printers, either through the RepRap Forums: https://forums.reprap.org or through IRC which can be accessed from here: https://reprappro.com/support-channel/ (works on Chrome, not Firefox).

Best regards,

RepRapPro Support Team.

dc42, 2015-11-01:
I just tested it in my fork, and M208 does limit the Z axis movement correctly, assuming of course the printer has been Z-homed and you do not use M564 to disable the limit. However, the current RepRapPro source code explicitly disables the check for the Z axis.

RRP-support, 2015-11-01:
This is an automated reply to your message "Re: [RepRapFirmware] M208 fails to set maximum Z movement (#86)" sent to support@reprappro.com.

Dear dc42 <notifications@github.com>

Thank you for your email. We endeavour to answer all emails within 24 hours. It may take longer during busy times, and holiday periods. We process all customer queries on a first come first served basis, during our office hours which are 9am to 5pm GMT Mon-Fri.

Other support channels are available. Please refer to the relevant troubleshooting guide for your machine:

Ormerod 2: https://reprappro.com/documentation/ormerod-2/troubleshooting/
Ormerod: https://reprappro.com/documentation/ormerod/troubleshooting/

Huxley Duo: https://reprappro.com/documentation/huxley-duo/troubleshooting/
Huxley: https://reprappro.com/documentation/huxley/troubleshooting/

Mono and Tricolour Mendel: https://reprappro.com/documentation/mendel-tricolour/troubleshooting/

Support is also available from other owners of RepRapPro and other 3D printers, either through the RepRap Forums: https://forums.reprap.org or through IRC which can be accessed from here: https://reprappro.com/support-channel/ (works on Chrome, not Firefox).

Best regards,

RepRapPro Support Team.

gratefulfrog, 2015-11-01:
Hi dc42,

Of course, I had Z-home before testing...

So you say that your fork corrects this problem as well as the Y compensation issue that I raised earlier?

I'd like to try your fork, could you please tell me where to get it and how to install it, and if there are any issues I should be aware of?

Cheers,
Bob

RRP-support, 2015-11-01:
This is an automated reply to your message "Re: [RepRapFirmware] M208 fails to set maximum Z movement (#86)" sent to support@reprappro.com.

Dear gratefulfrog <notifications@github.com>

Thank you for your email. We endeavour to answer all emails within 24 hours. It may take longer during busy times, and holiday periods. We process all customer queries on a first come first served basis, during our office hours which are 9am to 5pm GMT Mon-Fri.

Other support channels are available. Please refer to the relevant troubleshooting guide for your machine:

Ormerod 2: https://reprappro.com/documentation/ormerod-2/troubleshooting/
Ormerod: https://reprappro.com/documentation/ormerod/troubleshooting/

Huxley Duo: https://reprappro.com/documentation/huxley-duo/troubleshooting/
Huxley: https://reprappro.com/documentation/huxley/troubleshooting/

Mono and Tricolour Mendel: https://reprappro.com/documentation/mendel-tricolour/troubleshooting/

Support is also available from other owners of RepRapPro and other 3D printers, either through the RepRap Forums: https://forums.reprap.org or through IRC which can be accessed from here: https://reprappro.com/support-channel/ (works on Chrome, not Firefox).

Best regards,

RepRapPro Support Team.

dc42, 2015-11-02:
You can find my fork at
https://github.com/dc42/RepRapFirmware/tree/dev/Release. Follow the link
to the version you want (1.09k-dc42 is the latest) then click on Raw to
download it.

If your printer is an Ormerod 2 then your existing config.g file should
work with it. Otherwise, you may need to add a M574 line in config.g to
tell it what sort of homing switches you have. Also if you want to use
simultaneous X and Y homing then you need to use my homing files. See
http://reprap.org/wiki/Configuring_RepRapFirmware_for_a_Cartesian_printer for
more.

David Crocker, Escher Technologies Ltd.
http://www.eschertech.com
Tel. +44 (0)20 8144 3265 or +44 (0)7977 211486

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

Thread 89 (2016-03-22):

capability to control the ready to use cutting modules such as auto focus laser head or plasma THC

mkeyno, 2016-03-22:
hi , I was wondering if this firmware have capability to control the ready to use cutting modules such as auto focus laser head or plasma THC ,
I saw couple of effort on Marlin enthusiast to check output sensor the cutting tool and control the stepper motor the module to control height during the printing
any comments really appreciated

RRP-support, 2016-03-22:
This is an automated reply to your message "[RepRapFirmware] capability to control the ready to use cutting
 modules such as auto focus laser head or plasma THC  (#89)" sent to support@reprappro.com.

Dear mehrdad <notifications@github.com>

This is an automated reply to your message "[RepRapFirmware] capability to control the ready to use cutting
 modules such as auto focus laser head or plasma THC  (#89)" sent to support@reprappro.com.

Dear mehrdad <notifications@github.com>

RepRap Professional Ltd. is now closed.

Note that our closure does not affect RepRapPro China Ltd (http://www.reprappro.com.cn/). That is a completely separate company (though we have obviously worked closely with them) and they will continue.

The market for low-cost 3D printers is now so crowded and so competitive that a small specialist company like ours could not expand. So, because we were not bankrupt and we did not have any debts to pay, we chose to stop while we were ahead and to concentrate on other activities.

We are an open-source company. This means that all our designs, software source-code and documentation are freely available online on our website and on the Github link below. All that information will continue to be available into the future.

Here is a list of places to look if you want to get parts for RepRapPro's designs:

The RepRap.org Website (http://reprap.org/wiki/RepRap_Buyers'_Guide)

eMaker (http://www.emakershop.com/Seller=7244)

RepRap Ltd (http://reprapltd.com/)

RepRapPro China Ltd (http://www.reprappro.com.cn/)

Think3DPrint3D (https://www.think3dprint3d.com/)

Trapletshop (http://gb.trapletshop.com/fisher-delta-3d-printer)

Replikeo (http://www.replikeo.com/en/)

RS Components (http://uk.rs-online.com/web/)

Mouser (http://www.mouser.co.uk/)

Farnell (http://uk.farnell.com/)

Toby (http://www.toby.co.uk/)

Our designs (including those for all the 3D-printed parts) are all available here: Github

If you donâ��t have access to a 3D Printer to make the parts for our designs, try 3Dhubs or your local hackerspace or makerspace. The latter two will also almost certainly have a lasercutter that will make the sheet parts for our designs as well.

We would like to thank everyone who has supported us in the past, either as customers or as contributors who have improved our open-source products, or both. The fact that, unusually for a former company, we will be able to leave megabytes of useful information available to everyone in perpetuity is due in part to the support from those people.

Other support channels are available. Please refer to the relevant troubleshooting guide for your machine:

Ormerod 2: https://reprappro.com/documentation/ormerod-2/troubleshooting/
Ormerod: https://reprappro.com/documentation/ormerod/troubleshooting/

Huxley Duo: https://reprappro.com/documentation/huxley-duo/troubleshooting/
Huxley: https://reprappro.com/documentation/huxley/troubleshooting/

Mono and Tricolour Mendel: https://reprappro.com/documentation/mendel-tricolour/troubleshooting/

Support is also available from other owners of RepRapPro and other 3D printers, either through the RepRap Forums: https://forums.reprap.org or through IRC which can be accessed from here: https://reprappro.com/support-channel/ (works on Chrome, not Firefox).

Best regards,

RepRapPro Support Team.

dc42, 2016-03-22:
RepRapFirmware is now maintained by myself (dc42) and Christian Hammacher (chrishamm), with additional contributions from Dan Newman (who maintains the RADDS port) and Think3DPrint3D. Chris and I maintain separate forks but take most of each other's changes.

I believe the M571 command (http://reprap.org/wiki/G-code#M571:_Set_output_on_extrude) has been used to implement a laser engraver using RepRapFirmware.

RRP-support, 2016-03-22:
This is an automated reply to your message "Re: [RepRapFirmware] capability to control the ready to use cutting
 modules such as auto focus laser head or plasma THC  (#89)" sent to support@reprappro.com.

Dear dc42 <notifications@github.com>

This is an automated reply to your message "Re: [RepRapFirmware] capability to control the ready to use cutting
 modules such as auto focus laser head or plasma THC  (#89)" sent to support@reprappro.com.

Dear dc42 <notifications@github.com>

RepRap Professional Ltd. is now closed.

Note that our closure does not affect RepRapPro China Ltd (http://www.reprappro.com.cn/). That is a completely separate company (though we have obviously worked closely with them) and they will continue.

The market for low-cost 3D printers is now so crowded and so competitive that a small specialist company like ours could not expand. So, because we were not bankrupt and we did not have any debts to pay, we chose to stop while we were ahead and to concentrate on other activities.

We are an open-source company. This means that all our designs, software source-code and documentation are freely available online on our website and on the Github link below. All that information will continue to be available into the future.

Here is a list of places to look if you want to get parts for RepRapPro's designs:

The RepRap.org Website (http://reprap.org/wiki/RepRap_Buyers'_Guide)

eMaker (http://www.emakershop.com/Seller=7244)

RepRap Ltd (http://reprapltd.com/)

RepRapPro China Ltd (http://www.reprappro.com.cn/)

Think3DPrint3D (https://www.think3dprint3d.com/)

Trapletshop (http://gb.trapletshop.com/fisher-delta-3d-printer)

Replikeo (http://www.replikeo.com/en/)

RS Components (http://uk.rs-online.com/web/)

Mouser (http://www.mouser.co.uk/)

Farnell (http://uk.farnell.com/)

Toby (http://www.toby.co.uk/)

Our designs (including those for all the 3D-printed parts) are all available here: Github

If you donâ��t have access to a 3D Printer to make the parts for our designs, try 3Dhubs or your local hackerspace or makerspace. The latter two will also almost certainly have a lasercutter that will make the sheet parts for our designs as well.

We would like to thank everyone who has supported us in the past, either as customers or as contributors who have improved our open-source products, or both. The fact that, unusually for a former company, we will be able to leave megabytes of useful information available to everyone in perpetuity is due in part to the support from those people.

Other support channels are available. Please refer to the relevant troubleshooting guide for your machine:

Ormerod 2: https://reprappro.com/documentation/ormerod-2/troubleshooting/
Ormerod: https://reprappro.com/documentation/ormerod/troubleshooting/

Huxley Duo: https://reprappro.com/documentation/huxley-duo/troubleshooting/
Huxley: https://reprappro.com/documentation/huxley/troubleshooting/

Mono and Tricolour Mendel: https://reprappro.com/documentation/mendel-tricolour/troubleshooting/
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
mkeyno, 2016-03-28:
dear @dc42 can I have your idea about possibility of auto height control of CNC tools in the RRF?
Right now Manually  Control the laser head height is possible with Marlin function such as [action_laser_focus_custom(),](https://github.com/HakanBastedt/Marlin4Due/blob/Laser/Marlin/ultralcd.cpp#L106-L126)  and I think ,in two ways we can control the  tools heights  during printing our cutting
One with help  of separate modules and one is totally implemented  in firmware
In the first method (hard way) we could use the Arduino module to command the z axis whenever new bias with per set  g-code height come out, and when adjustment performed active the readiness pin  which is controlled by g-code M266 command before each  cutting
In the second way we could use the function such as [laser_set_focus(currentZ)](https://github.com/HakanBastedt/Marlin4Due/blob/Laser/Marlin/ultralcd.cpp#L1208) in loop function , in this case we need use I2C to request the height from sensor module

also I really appreciated to  have your colleagues comments

RRP-support, 2016-03-28:
This is an automated reply to your message "Re: [reprappro/RepRapFirmware] capability to control the ready to use
 cutting modules such as auto focus laser head or plasma THC  (#89)" sent to support@reprappro.com.

Dear mehrdad <notifications@github.com>

This is an automated reply to your message "Re: [reprappro/RepRapFirmware] capability to control the ready to use
 cutting modules such as auto focus laser head or plasma THC  (#89)" sent to support@reprappro.com.

Dear mehrdad <notifications@github.com>

RepRap Professional Ltd. is now closed.

Note that our closure does not affect RepRapPro China Ltd (http://www.reprappro.com.cn/). That is a completely separate company (though we have obviously worked closely with them) and they will continue.

The market for low-cost 3D printers is now so crowded and so competitive that a small specialist company like ours could not expand. So, because we were not bankrupt and we did not have any debts to pay, we chose to stop while we were ahead and to concentrate on other activities.

We are an open-source company. This means that all our designs, software source-code and documentation are freely available online on our website and on the Github link below. All that information will continue to be available into the future.

Here is a list of places to look if you want to get parts for RepRapPro's designs:

The RepRap.org Website (http://reprap.org/wiki/RepRap_Buyers'_Guide)

eMaker (http://www.emakershop.com/Seller=7244)

RepRap Ltd (http://reprapltd.com/)

RepRapPro China Ltd (http://www.reprappro.com.cn/)

Think3DPrint3D (https://www.think3dprint3d.com/)

Trapletshop (http://gb.trapletshop.com/fisher-delta-3d-printer)

Replikeo (http://www.replikeo.com/en/)

RS Components (http://uk.rs-online.com/web/)

Mouser (http://www.mouser.co.uk/)

Farnell (http://uk.farnell.com/)

Toby (http://www.toby.co.uk/)

Our designs (including those for all the 3D-printed parts) are all available here: Github

If you donâ��t have access to a 3D Printer to make the parts for our designs, try 3Dhubs or your local hackerspace or makerspace. The latter two will also almost certainly have a lasercutter that will make the sheet parts for our designs as well.

We would like to thank everyone who has supported us in the past, either as customers or as contributors who have improved our open-source products, or both. The fact that, unusually for a former company, we will be able to leave megabytes of useful information available to everyone in perpetuity is due in part to the support from those people.

Other support channels are available. Please refer to the relevant troubleshooting guide for your machine:

Ormerod 2: https://reprappro.com/documentation/ormerod-2/troubleshooting/
Ormerod: https://reprappro.com/documentation/ormerod/troubleshooting/

Huxley Duo: https://reprappro.com/documentation/huxley-duo/troubleshooting/
Huxley: https://reprappro.com/documentation/huxley/troubleshooting/

Mono and Tricolour Mendel: https://reprappro.com/documentation/mendel-tricolour/troubleshooting/

Support is also available from other owners of RepRapPro and other 3D printers, either through the RepRap Forums: https://forums.reprap.org or through IRC which can be accessed from here: https://reprappro.com/support-channel/ (works on Chrome, not Firefox).

Best regards,

RepRapPro Support Team.

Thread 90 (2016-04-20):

X endstop always pressed after M569 code

Graeme84, 2016-04-20:
I am working with the build of the software in the `Release` directory and have edited the default `config.g` file that came on the SD card supplied with a Duet 0.8.5 board have bought from Think3dPrint3d.

The default `config.g` file contains configurations for 6 extruders. Even thought I am only using one, I did not see any harm in keeping the other configurations. However, when using the file I found a problem where the software would always behave as though the endstop was pressed. This was not the case when I switched on the board without an SD card present.

Executing the configuration codes one by one, I found the issue began after `M569 P8 S1` (configuring the direction of the 6th extruder). Below is the `pronsole` output of the issue being reproduced, no endstops were pressed during the execution of the codes:

    PC> M119
    SENDING:M119
    Endstops - X: not stopped, Y: at max stop, Z: not stopped
    PC> M569 P8 S1
    SENDING:M569 P8 S1
    PC> M119
    SENDING:M119
    Endstops - X: at min stop, Y: at max stop, Z: not stopped

RRP-support, 2016-04-20:
This is an automated reply to your message "[reprappro/RepRapFirmware] X endstop always pressed after M569 code
 (#90)" sent to support@reprappro.com.

Dear Graeme84 <notifications@github.com>

This is an automated reply to your message "[reprappro/RepRapFirmware] X endstop always pressed after M569 code
 (#90)" sent to support@reprappro.com.

Dear Graeme84 <notifications@github.com>

RepRap Professional Ltd. is now closed.

Note that our closure does not affect RepRapPro China Ltd (http://www.reprappro.com.cn/). That is a completely separate company (though we have obviously worked closely with them) and they will continue.

The market for low-cost 3D printers is now so crowded and so competitive that a small specialist company like ours could not expand. So, because we were not bankrupt and we did not have any debts to pay, we chose to stop while we were ahead and to concentrate on other activities.

We are an open-source company. This means that all our designs, software source-code and documentation are freely available online on our website and on the Github link below. All that information will continue to be available into the future.

Here is a list of places to look if you want to get parts for RepRapPro's designs:

The RepRap.org Website (http://reprap.org/wiki/RepRap_Buyers'_Guide)

eMaker (http://www.emakershop.com/Seller=7244)

RepRap Ltd (http://reprapltd.com/)

RepRapPro China Ltd (http://www.reprappro.com.cn/)

Think3DPrint3D (https://www.think3dprint3d.com/)

Trapletshop (http://gb.trapletshop.com/fisher-delta-3d-printer)

Replikeo (http://www.replikeo.com/en/)

RS Components (http://uk.rs-online.com/web/)

Mouser (http://www.mouser.co.uk/)

Farnell (http://uk.farnell.com/)

Toby (http://www.toby.co.uk/)

Our designs (including those for all the 3D-printed parts) are all available here: Github

If you donâ��t have access to a 3D Printer to make the parts for our designs, try 3Dhubs or your local hackerspace or makerspace. The latter two will also almost certainly have a lasercutter that will make the sheet parts for our designs as well.

We would like to thank everyone who has supported us in the past, either as customers or as contributors who have improved our open-source products, or both. The fact that, unusually for a former company, we will be able to leave megabytes of useful information available to everyone in perpetuity is due in part to the support from those people.

Other support channels are available. Please refer to the relevant troubleshooting guide for your machine:

Ormerod 2: https://reprappro.com/documentation/ormerod-2/troubleshooting/
Ormerod: https://reprappro.com/documentation/ormerod/troubleshooting/

Huxley Duo: https://reprappro.com/documentation/huxley-duo/troubleshooting/
Huxley: https://reprappro.com/documentation/huxley/troubleshooting/

Mono and Tricolour Mendel: https://reprappro.com/documentation/mendel-tricolour/troubleshooting/

Support is also available from other owners of RepRapPro and other 3D printers, either through the RepRap Forums: https://forums.reprap.org or through IRC which can be accessed from here: https://reprappro.com/support-channel/ (works on Chrome, not Firefox).

Best regards,

RepRapPro Support Team.

dc42, 2016-04-20:
Hi Gramme,  the RepRapPro build is very old and predates the Duet 0.8.5 board. I suggest you use my fork or chrishamm's. You can find mine at github.com/dc42/RepRapFirmware. Regards David

RRP-support, 2016-04-20:
This is an automated reply to your message "Re: [reprappro/RepRapFirmware] X endstop always pressed after M569
 code (#90)" sent to support@reprappro.com.

Dear dc42 <notifications@github.com>

This is an automated reply to your message "Re: [reprappro/RepRapFirmware] X endstop always pressed after M569
 code (#90)" sent to support@reprappro.com.

Dear dc42 <notifications@github.com>

RepRap Professional Ltd. is now closed.

Note that our closure does not affect RepRapPro China Ltd (http://www.reprappro.com.cn/). That is a completely separate company (though we have obviously worked closely with them) and they will continue.

The market for low-cost 3D printers is now so crowded and so competitive that a small specialist company like ours could not expand. So, because we were not bankrupt and we did not have any debts to pay, we chose to stop while we were ahead and to concentrate on other activities.

We are an open-source company. This means that all our designs, software source-code and documentation are freely available online on our website and on the Github link below. All that information will continue to be available into the future.

Here is a list of places to look if you want to get parts for RepRapPro's designs:

The RepRap.org Website (http://reprap.org/wiki/RepRap_Buyers'_Guide)

eMaker (http://www.emakershop.com/Seller=7244)

RepRap Ltd (http://reprapltd.com/)

RepRapPro China Ltd (http://www.reprappro.com.cn/)

Think3DPrint3D (https://www.think3dprint3d.com/)

Trapletshop (http://gb.trapletshop.com/fisher-delta-3d-printer)

Replikeo (http://www.replikeo.com/en/)

RS Components (http://uk.rs-online.com/web/)

Mouser (http://www.mouser.co.uk/)

Farnell (http://uk.farnell.com/)

Toby (http://www.toby.co.uk/)

Our designs (including those for all the 3D-printed parts) are all available here: Github

If you donâ��t have access to a 3D Printer to make the parts for our designs, try 3Dhubs or your local hackerspace or makerspace. The latter two will also almost certainly have a lasercutter that will make the sheet parts for our designs as well.

We would like to thank everyone who has supported us in the past, either as customers or as contributors who have improved our open-source products, or both. The fact that, unusually for a former company, we will be able to leave megabytes of useful information available to everyone in perpetuity is due in part to the support from those people.

Other support channels are available. Please refer to the relevant troubleshooting guide for your machine:

Ormerod 2: https://reprappro.com/documentation/ormerod-2/troubleshooting/
Ormerod: https://reprappro.com/documentation/ormerod/troubleshooting/

Huxley Duo: https://reprappro.com/documentation/huxley-duo/troubleshooting/
Huxley: https://reprappro.com/documentation/huxley/troubleshooting/

Mono and Tricolour Mendel: https://reprappro.com/documentation/mendel-tricolour/troubleshooting/

Support is also available from other owners of RepRapPro and other 3D printers, either through the RepRap Forums: https://forums.reprap.org or through IRC which can be accessed from here: https://reprappro.com/support-channel/ (works on Chrome, not Firefox).

Best regards,

RepRapPro Support Team.

Graeme84, 2016-04-20:
Ok, thanks David. I see that there are a lot of forks of this software!

RRP-support, 2016-04-20:
This is an automated reply to your message "Re: [reprappro/RepRapFirmware] X endstop always pressed after M569
 code (#90)" sent to support@reprappro.com.

Dear Graeme84 <notifications@github.com>

This is an automated reply to your message "Re: [reprappro/RepRapFirmware] X endstop always pressed after M569
 code (#90)" sent to support@reprappro.com.

Dear Graeme84 <notifications@github.com>

RepRap Professional Ltd. is now closed.

Note that our closure does not affect RepRapPro China Ltd (http://www.reprappro.com.cn/). That is a completely separate company (though we have obviously worked closely with them) and they will continue.

The market for low-cost 3D printers is now so crowded and so competitive that a small specialist company like ours could not expand. So, because we were not bankrupt and we did not have any debts to pay, we chose to stop while we were ahead and to concentrate on other activities.

We are an open-source company. This means that all our designs, software source-code and documentation are freely available online on our website and on the Github link below. All that information will continue to be available into the future.

Here is a list of places to look if you want to get parts for RepRapPro's designs:

The RepRap.org Website (http://reprap.org/wiki/RepRap_Buyers'_Guide)

eMaker (http://www.emakershop.com/Seller=7244)

RepRap Ltd (http://reprapltd.com/)

RepRapPro China Ltd (http://www.reprappro.com.cn/)

Think3DPrint3D (https://www.think3dprint3d.com/)

Trapletshop (http://gb.trapletshop.com/fisher-delta-3d-printer)

Replikeo (http://www.replikeo.com/en/)

RS Components (http://uk.rs-online.com/web/)

Mouser (http://www.mouser.co.uk/)

Farnell (http://uk.farnell.com/)

Toby (http://www.toby.co.uk/)

Our designs (including those for all the 3D-printed parts) are all available here: Github

If you donâ��t have access to a 3D Printer to make the parts for our designs, try 3Dhubs or your local hackerspace or makerspace. The latter two will also almost certainly have a lasercutter that will make the sheet parts for our designs as well.

We would like to thank everyone who has supported us in the past, either as customers or as contributors who have improved our open-source products, or both. The fact that, unusually for a former company, we will be able to leave megabytes of useful information available to everyone in perpetuity is due in part to the support from those people.

Other support channels are available. Please refer to the relevant troubleshooting guide for your machine:

Ormerod 2: https://reprappro.com/documentation/ormerod-2/troubleshooting/
Ormerod: https://reprappro.com/documentation/ormerod/troubleshooting/

Huxley Duo: https://reprappro.com/documentation/huxley-duo/troubleshooting/
Huxley: https://reprappro.com/documentation/huxley/troubleshooting/

Mono and Tricolour Mendel: https://reprappro.com/documentation/mendel-tricolour/troubleshooting/

Support is also available from other owners of RepRapPro and other 3D printers, either through the RepRap Forums: https://forums.reprap.org or through IRC which can be accessed from here: https://reprappro.com/support-channel/ (works on Chrome, not Firefox).

Best regards,

RepRapPro Support Team.

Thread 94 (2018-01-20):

inverse the direction of the Z motor

Lepterois, 2018-01-20:
Hi!
I changed today my Z scew on my Ormerod2.
But now the direction of the scew is inverted, and as a newbie, I don't know witch Gcode I've to put in my config.g. Actually in my config.g, I've M569 P0 S0 to set the X axis direction, I guess that the same for Z but I didn't find M569 in the wikicode.... and I don't know what is the number of Z motor? Is it P2?
As well how to adjust in the config.g the step/mm for my Z?

Thanks in advance

Lepterois, 2018-01-20:
OK I found to reverse.... M569 P2 S0
Still to adjust the step/mm

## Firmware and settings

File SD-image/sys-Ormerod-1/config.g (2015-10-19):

; Configuration file for RepRap Ormerod 1
; RepRapPro Ltd
;
; Copy this file to config.g if you have an Ormerod 1
; If you are updating a config.g that you already have you
; may wish to go through it and this file checking what you
; want to keep from your old file.
; 
; For G-code definitions, see http://reprap.org/wiki/G-code
; 
M111 S0                             ; Debug off
M550 PMy RepRapPro Ormerod 1        ; Machine name (can be anything you like). With DHCP enabled connect to (example) http://reprapproormerod1 (machine name with no spaces).
M551 Preprap                        ; Machine password (currently not used)
M540 P0xBE:0xEF:0xDE:0xAD:0xFE:0xED ; MAC Address
;M552 P0.0.0.0                       ; Un-comment for DHCP
M552 P192.168.1.14                  ; IP address, comment for DHCP
M553 P255.255.255.0                 ; Netmask
M554 P192.168.1.1                   ; Gateway, comment for DHCP
M555 P2                             ; Set output to look like Marlin
G21                                 ; Work in millimetres
G90                                 ; Send absolute corrdinates...
M83                                 ; ...but relative extruder moves
M574 X0 Y2 Z0 S1                    ; set endstop configuration (Y endstop only, at high end, active high)
M906 X800 Y1000 Z800 E1000          ; Set motor currents (mA)
;M305 P0 R4700 H0 L0                 ; Set the heated bed thermistor series resistor to 4K7
;M305 P1 R4700 H0 L0                 ; Set the hot end thermistor series resistor to 4K7
;M305 P2 R4700 H0 L0                 ; Set the second hot end thermistor series resistor to 4K7
M569 P0 S1                          ; Reverse the X axis
M92 E420:420                        ; Set extruder steps per mm
M558 P1                             ; Use an unmodulated Z probe
G31 Z0.8 P600                       ; Set the probe height and threshold (deliberately too high to avoid bed crashes on initial setup)
M556 S78 X0 Y0 Z0                   ; Put your axis compensation here
M201 X1000 Y1000 Z20 E1000          ; Accelerations (mm/s^2)
M203 X15000 Y15000 Z180 E3600       ; Maximum speeds (mm/min)
M566 X1800 Y1800 Z30 E20            ; Maximum instantaneous speed changes mm/minute
M208 X-24 S1                        ; Set axis minimum (adjust to make X=0 the edge of the bed)
M208 X214 Y210                      ; Set axis maxima (adjust to suit your machine)
M563 P0 D0 H1                       ; Define tool 0
G10 P0 S-273 R-273                  ; Set tool 0 operating and standby temperatures
;M563 P1 D1 H2                          ; Define tool 1 Uncomment if you have a dual colour upgrade
;G10 P1 X19 S-273 R-273                ; Set tool 1 operating and standby temperatures  Uncomment if you have a dual colour upgrade

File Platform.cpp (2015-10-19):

/****************************************************************************************************

 RepRapFirmware - Platform: RepRapPro Ormerod with Arduino Due controller

 Platform contains all the code and definitions to deal with machine-dependent things such as control
 pins, bed area, number of extruders, tolerable accelerations and speeds and so on.

 -----------------------------------------------------------------------------------------------------

 Version 0.1

 18 November 2012

 Adrian Bowyer
 RepRap Professional Ltd
 http://reprappro.com

 Licence: GPL

 ****************************************************************************************************/

#include "RepRapFirmware.h"
#include "DueFlashStorage.h"

extern char _end;
extern "C" char *sbrk(int i);

const uint8_t memPattern = 0xA5;
const int Dac0DigitalPin = 66;						// Arduino Due pin number corresponding to DAC0 output pin

static uint32_t fanInterruptCount = 0;				// accessed only in ISR, so no need to declare it volatile
const uint32_t fanMaxInterruptCount = 32;			// number of fan interrupts that we average over
static volatile uint32_t fanLastResetTime = 0;		// time (microseconds) at which we last reset the interrupt count, accessed inside and outside ISR
static volatile uint32_t fanInterval = 0;			// written by ISR, read outside the ISR

//#define MOVE_DEBUG

#ifdef MOVE_DEBUG
unsigned int numInterruptsScheduled = 0;
unsigned int numInterruptsExecuted = 0;
uint32_t nextInterruptTime = 0;
uint32_t nextInterruptScheduledAt = 0;
uint32_t lastInterruptTime = 0;
#endif

// Arduino initialise and loop functions
// Put nothing in these other than calls to the RepRap equivalents

void setup()
{
	// Fill the free memory with a pattern so that we can check for stack usage and memory corruption
	char* heapend = sbrk(0);
	register const char * stack_ptr asm ("sp");
	while (heapend + 16 < stack_ptr)
	{
		*heapend++ = memPattern;
	}

	reprap.Init();
}

void loop()
{
	reprap.Spin();
}

extern "C"
{
	// This intercepts the 1ms system tick. It must return 'false', otherwise the Arduino core tick handler will be bypassed.
	int sysTickHook()
	{
		reprap.Tick();
		return 0;
	}
}

void watchdogSetup(void)
{
    // RepRapFirmware enables the watchdog by default
    watchdogEnable(1000);
}

//*************************************************************************************************
// PidParameters class

bool PidParameters::UsePID() const
{
	return kP >= 0;
}

float PidParameters::GetThermistorR25() const
{
	return thermistorInfR * exp(thermistorBeta / (25.0 - ABS_ZERO));
}

void PidParameters::SetThermistorR25AndBeta(float r25, float beta)
{
	thermistorInfR = r25 * exp(-beta / (25.0 - ABS_ZERO));
	thermistorBeta = beta;
}

bool PidParameters::operator==(const PidParameters& other) const
{
	return kI == other.kI && kD == other.kD && kP == other.kP && kT == other.kT && kS == other.kS
				&& fullBand == other.fullBand && pidMin == other.pidMin
				&& pidMax == other.pidMax && thermistorBeta == other.thermistorBeta && thermistorInfR == other.thermistorInfR
				&& thermistorSeriesR == other.thermistorSeriesR && adcLowOffset == other.adcLowOffset
				&& adcHighOffset == other.adcHighOffset;
}

//*******************************************************************************************************************
// Platform class

Platform::Platform() :
		autoSaveEnabled(false), board(BoardType::Duet_06), active(false), errorCodeBits(0), auxOutputBuffer(nullptr), aux2OutputBuffer(nullptr),
		usbOutputBuffer(nullptr), fileStructureInitialised(false), tickState(0), debugCode(0)
{
	// Files

	massStorage = new MassStorage(this);

	for(size_t i = 0; i < MAX_FILES; i++)
	{
		files[i] = new FileStore(this);
	}
}

//*******************************************************************************************************************

void Platform::Init()
{
	// Deal with power first
	digitalWrite(atxPowerPin, LOW);		// ensure ATX power is off by default
	pinMode(atxPowerPin, OUTPUT);

	SetBoardType(BoardType::Auto);

	// Comms
	baudRates[0] = USB_BAUD_RATE;
	baudRates[1] = AUX_BAUD_RATE;
	baudRates[2] = AUX2_BAUD_RATE;
	commsParams[0] = 0;
	commsParams[1] = 1;							// by default we require a checksum on data from the aux port, to guard against overrun errors
	// Third serial channel isn't a G-Code source

	SerialUSB.begin(baudRates[0]);
	Serial.begin(baudRates[1]);					// this can't be done in the constructor because the Arduino port initialisation isn't complete at that point
	Serial1.begin(baudRates[2]);

	static_assert(sizeof(FlashData) + sizeof(SoftwareResetData) <= 1024, "NVData too large");

	ResetNvData();

	// We need to initialise at least some of the time stuff before we call MassStorage::Init()
	addToTime = 0.0;
	lastTimeCall = 0;
	lastTime = Time();
	longWait = lastTime;

	// File management
	massStorage->Init();

	for(size_t file = 0; file < MAX_FILES; file++)
	{
		files[file]->Init();
	}

	fileStructureInitialised = true;

	mcpDuet.begin(); //only call begin once in the entire execution, this begins the I2C comms on that channel for all objects
	mcpExpansion.setMCP4461Address(0x2E); //not required for mcpDuet, as this uses the default address
	sysDir = SYS_DIR;
	macroDir = MACRO_DIR;
	configFile = CONFIG_FILE;
	defaultFile = DEFAULT_FILE;

	// DRIVES
	ARRAY_INIT(stepPins, STEP_PINS);
	ARRAY_INIT(directionPins, DIRECTION_PINS);
	ARRAY_INIT(directions, DIRECTIONS);
	ARRAY_INIT(enableValues, ENABLE_VALUES);
	ARRAY_INIT(enablePins, ENABLE_PINS);
	ARRAY_INIT(endStopPins, END_STOP_PINS);
	ARRAY_INIT(maxFeedrates, MAX_FEEDRATES);
	ARRAY_INIT(accelerations, ACCELERATIONS);
	ARRAY_INIT(driveStepsPerUnit, DRIVE_STEPS_PER_UNIT);
	ARRAY_INIT(instantDvs, INSTANT_DVS);
	ARRAY_INIT(potWipes, POT_WIPES);

	senseResistor = SENSE_RESISTOR;
	maxStepperDigipotVoltage = MAX_STEPPER_DIGIPOT_VOLTAGE;
	maxStepperDACVoltage = MAX_STEPPER_DAC_VOLTAGE;

	// Z PROBE

	zProbePin = Z_PROBE_PIN;
	zProbeAdcChannel = PinToAdcChannel(zProbePin);
	InitZProbe();		// this also sets up zProbeModulationPin

	// AXES

	ARRAY_INIT(axisMaxima, AXIS_MAXIMA);
	ARRAY_INIT(axisMinima, AXIS_MINIMA);

	idleCurrentFactor = DEFAULT_IDLE_CURRENT_FACTOR;
	SetSlowestDrive();

	// HEATERS - Bed is assumed to be the first

	ARRAY_INIT(tempSensePins, TEMP_SENSE_PINS);
	ARRAY_INIT(heatOnPins, HEAT_ON_PINS);
	ARRAY_INIT(standbyTemperatures, STANDBY_TEMPERATURES);
	ARRAY_INIT(activeTemperatures, ACTIVE_TEMPERATURES);

	heatSampleTime = HEAT_SAMPLE_TIME;
	coolingFan0Value = 0.0;
	coolingFan1Value = 0.0;
	coolingFan0Pin = COOLING_FAN0_PIN;
	coolingFan1Pin = COOLING_FAN1_PIN;
	coolingFanRpmPin = COOLING_FAN_RPM_PIN;
	timeToHot = TIME_TO_HOT;
	lastRpmResetTime = 0.0;

	webDir = WEB_DIR;
	gcodeDir = GCODE_DIR;

	// Motors

	for(size_t drive = 0; drive < DRIVES; drive++)
	{
		SetPhysicalDrive(drive, drive);                                 // map drivers directly to axes and extruders
		if (stepPins[drive] >= 0)
		{
			pinMode(stepPins[drive], OUTPUT);
		}
		if (directionPins[drive] >= 0)
		{
			pinMode(directionPins[drive], OUTPUT);
		}
		if (enablePins[drive] >= 0)
		{
			pinMode(enablePins[drive], OUTPUT);
		}
		if (endStopPins[drive] >= 0)
		{
			pinMode(endStopPins[drive], INPUT_PULLUP);
		}
		motorCurrents[drive] = 0.0;
		DisableDrive(drive);
		driveState[drive] = DriveStatus::disabled;
		SetElasticComp(drive, 0.0);
		if (drive <= AXES)
		{
			endStopType[drive] = (drive == Y_AXIS)
									? EndStopType::lowEndStop	// for Ormerod 2/Huxley/Mendel compatibility
									: EndStopType::noEndStop;	// for Ormerod/Huxley/Mendel compatibility
			endStopLogicLevel[drive] = true;					// assume all endstops use active high logic e.g. normally-closed switch to ground
		}
	}

	extrusionAncilliaryPWM = 0.0;

	for(size_t heater = 0; heater < HEATERS; heater++)
	{
		if (heatOnPins[heater] >= 0)
		{
			digitalWrite(heatOnPins[heater], HIGH);	// turn the heater off
			pinMode(heatOnPins[heater], OUTPUT);
		}
		analogReadResolution(12);
		thermistorFilters[heater].Init(analogRead(tempSensePins[heater]));
		heaterAdcChannels[heater] = PinToAdcChannel(tempSensePins[heater]);

		// Calculate and store the ADC average sum that corresponds to an overheat condition, so that we can check is quickly in the tick ISR
		float thermistorOverheatResistance = nvData.pidParams[heater].GetRInf()
				* exp(-nvData.pidParams[heater].GetBeta() / (BAD_HIGH_TEMPERATURE - ABS_ZERO));
		float thermistorOverheatAdcValue = (AD_RANGE_REAL + 1) * thermistorOverheatResistance
				/ (thermistorOverheatResistance + nvData.pidParams[heater].thermistorSeriesR);
		thermistorOverheatSums[heater] = (uint32_t) (thermistorOverheatAdcValue + 0.9) * THERMISTOR_AVERAGE_READINGS;
	}

	if (coolingFan0Pin >= 0)
	{
		// Inverse logic for Duet v0.6 and later; this turns it off
		analogWriteDuet(coolingFan0Pin, (HEAT_ON == 0) ? 255 : 0, true);
	}
	if (coolingFan1Pin >= 0)
	{
		// Same here
		analogWriteDuet(coolingFan1Pin, (HEAT_ON == 0) ? 255 : 0, true);
	}
	if (coolingFanRpmPin >= 0)
	{
		pinModeDuet(coolingFanRpmPin, INPUT_PULLUP, 1500);
	}

	// Hotend configuration
	nozzleDiameter = NOZZLE_DIAMETER;
	filamentWidth = FILAMENT_WIDTH;

	// Inkjet

	inkjetBits = INKJET_BITS;
	if (inkjetBits >= 0)
	{
		inkjetFireMicroseconds = INKJET_FIRE_MICROSECONDS;
		inkjetDelayMicroseconds = INKJET_DELAY_MICROSECONDS;

		inkjetSerialOut = INKJET_SERIAL_OUT;
		pinMode(inkjetSerialOut, OUTPUT);
		digitalWrite(inkjetSerialOut, 0);

		inkjetShiftClock = INKJET_SHIFT_CLOCK;
		pinMode(inkjetShiftClock, OUTPUT);
		digitalWrite(inkjetShiftClock, LOW);

		inkjetStorageClock = INKJET_STORAGE_CLOCK;
		pinMode(inkjetStorageClock, OUTPUT);
		digitalWrite(inkjetStorageClock, LOW);

		inkjetOutputEnable = INKJET_OUTPUT_ENABLE;
		pinMode(inkjetOutputEnable, OUTPUT);
		digitalWrite(inkjetOutputEnable, HIGH);

		inkjetClear = INKJET_CLEAR;
		pinMode(inkjetClear, OUTPUT);
		digitalWrite(inkjetClear, HIGH);
	}

	// Get the show on the road...
	lastTime = Time();
	longWait = lastTime;
	InitialiseInterrupts();		// also sets 'active' to true
}

// Specify which thermistor channel a particular heater uses
void Platform::SetThermistorNumber(size_t heater, size_t thermistor)
{
	if (heater < HEATERS && thermistor < ARRAY_SIZE(tempSensePins))
	{
		heaterAdcChannels[heater] = PinToAdcChannel(tempSensePins[thermistor]);
	}
}

int Platform::GetThermistorNumber(size_t heater) const
{
	if (heater < HEATERS)
	{
		for(size_t thermistor = 0; thermistor < HEATERS; ++thermistor)
		{
			if (heaterAdcChannels[heater] == PinToAdcChannel(tempSensePins[thermistor]))
			{
				return thermistor;
			}
		}
	}
	return -1;
}

void Platform::SetSlowestDrive()
{
	slowestDrive = 0;
	for(size_t drive = 1; drive < DRIVES; drive++)
	{
		if (ConfiguredInstantDv(drive) < ConfiguredInstantDv(slowestDrive))
		{
			slowestDrive = drive;
		}
	}
}

void Platform::InitZProbe()
{
	zProbeOnFilter.Init(0);
	zProbeOffFilter.Init(0);
	zProbeModulationPin = (board == BoardType::Duet_07) ? Z_PROBE_MOD_PIN07 : Z_PROBE_MOD_PIN;

	if (nvData.zProbeType >= 1 && nvData.zProbeType <= 3)
	{
		pinMode(zProbeModulationPin, OUTPUT);
		digitalWrite(zProbeModulationPin, (nvData.zProbeType <= 2) ? HIGH : LOW);	// enable the IR LED or alternate sensor
	}
	else if (nvData.zProbeType == 4)
	{
		pinMode(endStopPins[E0_AXIS], INPUT_PULLUP);
	}
}

uint16_t Platform::GetRawZProbeReading() const
{
	if (nvData.zProbeType == 4)
	{
		bool b = (bool)digitalRead(endStopPins[E0_AXIS]);
		if (!endStopLogicLevel[AXES])
		{
			b = !b;
		}
		return (b) ? 4000 : 0;
	}
	else
	{
		return GetAdcReading(zProbeAdcChannel);
	}
}

// Return the Z probe data.
// The ADC readings are 12 bits, so we convert them to 10-bit readings for compatibility with the old firmware.
int Platform::ZProbe() const
{
	if (zProbeOnFilter.IsValid() && zProbeOffFilter.IsValid())
	{
		switch (nvData.zProbeType)
		{
			case 1:		// Simple or intelligent IR sensor
			case 3:		// Alternate sensor
			case 4:		// Mechanical Z probe
				return (int) ((zProbeOnFilter.GetSum() + zProbeOffFilter.GetSum()) / (8 * Z_PROBE_AVERAGE_READINGS));

			case 2:
				// Modulated IR sensor. We assume that zProbeOnFilter and zprobeOffFilter average the same number of readings.
				// Because of noise, it is possible to get a negative reading, so allow for this.
				return (int) (((int32_t) zProbeOnFilter.GetSum() - (int32_t) zProbeOffFilter.GetSum())
						/ (int)(4 * Z_PROBE_AVERAGE_READINGS));

			default:
				break;
		}
	}
	return 0;	// Z probe not turned on or not initialised yet
}

// Provide the Z probe secondary values and return the number of secondary values
int Platform::GetZProbeSecondaryValues(int& v1, int& v2)
{
	if (zProbeOnFilter.IsValid() && zProbeOffFilter.IsValid())
	{
		switch (nvData.zProbeType)
		{
			case 2:		// modulated IR sensor
				v1 = (int) (zProbeOnFilter.GetSum() / (4 * Z_PROBE_AVERAGE_READINGS));	// pass back the reading with IR turned on
				return 1;

			default:
				break;
		}
	}
	return 0;
}

int Platform::GetZProbeType() const
{
	return nvData.zProbeType;
}

void Platform::SetZProbeAxes(const bool axes[AXES])
{
	for(size_t axis=0; axis<AXES; axis++)
	{
		nvData.zProbeAxes[axis] = axes[axis];
	}

	if (autoSaveEnabled)
	{
		WriteNvData();
	}
}

void Platform::GetZProbeAxes(bool (&axes)[AXES])
{
	for(size_t axis=0; axis<AXES; axis++)
	{
		axes[axis] = nvData.zProbeAxes[axis];
	}
}

float Platform::ZProbeStopHeight() const
{
	switch (nvData.zProbeType)
	{
		case 0:
		case 4:
			return nvData.switchZProbeParameters.GetStopHeight(GetTemperature(0));
		case 1:
		case 2:
			return nvData.irZProbeParameters.GetStopHeight(GetTemperature(0));
		case 3:
			return nvData.alternateZProbeParameters.GetStopHeight(GetTemperature(0));
		default:
			return 0;
	}
}

float Platform::GetZProbeDiveHeight() const
{
	switch (nvData.zProbeType)
	{
		case 0:
		case 4:
			return nvData.switchZProbeParameters.diveHeight;
		case 1:
		case 2:
			return nvData.irZProbeParameters.diveHeight;
		case 3:
			return nvData.alternateZProbeParameters.diveHeight;
	}
	return DEFAULT_Z_DIVE;
}

float Platform::GetZProbeTravelSpeed() const
{
	switch (nvData.zProbeType)
	{
		case 0:
		case 4:
			return nvData.switchZProbeParameters.travelSpeed;
		case 1:
		case 2:
			return nvData.irZProbeParameters.travelSpeed;
		case 3:
			return nvData.alternateZProbeParameters.travelSpeed;
	}

	return DEFAULT_TRAVEL_SPEED;
}

void Platform::SetZProbeType(int pt)
{
	int newZProbeType = (pt >= 0 && pt <= 4) ? pt : 0;
	if (newZProbeType != nvData.zProbeType)
	{
		nvData.zProbeType = newZProbeType;
		if (autoSaveEnabled)
		{
			WriteNvData();
		}
	}
	InitZProbe();
}

const ZProbeParameters& Platform::GetZProbeParameters() const
{
	switch (nvData.zProbeType)
	{
		case 0:
		case 4:
		default:
			return nvData.switchZProbeParameters;

		case 1:
		case 2:
			return nvData.irZProbeParameters;

		case 3:
			return nvData.alternateZProbeParameters;
	}
}

bool Platform::SetZProbeParameters(const struct ZProbeParameters& params)
{
	switch (nvData.zProbeType)
	{
		case 0:
		case 4:
			if (nvData.switchZProbeParameters != params)
			{
				nvData.switchZProbeParameters = params;
				if (autoSaveEnabled)
				{
					WriteNvData();
				}
			}
			return true;

		case 1:
		case 2:
			if (nvData.irZProbeParameters != params)
			{
				nvData.irZProbeParameters = params;
				if (autoSaveEnabled)
				{
					WriteNvData();
				}
			}
			return true;

		case 3:
			if (nvData.alternateZProbeParameters != params)
			{
				nvData.alternateZProbeParameters = params;
				if (autoSaveEnabled)
				{
					WriteNvData();
				}
			}
			return true;
	}
	return false;
}

// Return true if we must home X and Y before we home Z (i.e. we are using a bed probe)
bool Platform::MustHomeXYBeforeZ() const
{
	return nvData.zProbeType != 0;
}

void Platform::ResetNvData()
{
	nvData.compatibility = me;

	ARRAY_INIT(nvData.ipAddress, IP_ADDRESS);
	ARRAY_INIT(nvData.netMask, NET_MASK);
	ARRAY_INIT(nvData.gateWay, GATE_WAY);
	ARRAY_INIT(nvData.macAddress, MAC_ADDRESS);

	nvData.zProbeType = 0;			// Default is to use the switch
	ARRAY_INIT(nvData.zProbeAxes, Z_PROBE_AXES);
	nvData.switchZProbeParameters.Init(0.0);
	nvData.irZProbeParameters.Init(Z_PROBE_STOP_HEIGHT);
	nvData.alternateZProbeParameters.Init(Z_PROBE_STOP_HEIGHT);

	for (size_t i = 0; i < HEATERS; ++i)
	{
		PidParameters& pp = nvData.pidParams[i];
		pp.thermistorSeriesR = DEFAULT_THERMISTOR_SERIES_RS[i];
		pp.SetThermistorR25AndBeta(DEFAULT_THERMISTOR_25_RS[i], DEFAULT_THERMISTOR_BETAS[i]);
		pp.kI = DEFAULT_PID_KIS[i];
		pp.kD = DEFAULT_PID_KDS[i];
		pp.kP = DEFAULT_PID_KPS[i];
		pp.kT = DEFAULT_PID_KTS[i];
		pp.kS = DEFAULT_PID_KSS[i];
		pp.fullBand = DEFAULT_PID_FULLBANDS[i];
		pp.pidMin = DEFAULT_PID_MINS[i];
		pp.pidMax = DEFAULT_PID_MAXES[i];
		pp.adcLowOffset = pp.adcHighOffset = 0.0;
	}

#ifdef FLASH_SAVE_ENABLED
	nvData.magic = FlashData::magicValue;
#endif
}

void Platform::ReadNvData()
{
#ifdef FLASH_SAVE_ENABLED
	DueFlashStorage::read(FlashData::nvAddress, &nvData, sizeof(nvData));
	if (nvData.magic != FlashData::magicValue)
	{
		// Nonvolatile data has not been initialised since the firmware was last written, so set up default values
		ResetNvData();
		// No point in writing it back here
	}
#else
	Message(GENERIC_MESSAGE, "Error: Cannot load non-volatile data, because Flash support has been disabled!\n");
#endif
}

void Platform::WriteNvData()
{
#ifdef FLASH_SAVE_ENABLED
	DueFlashStorage::write(FlashData::nvAddress, &nvData, sizeof(nvData));
#else
	Message(GENERIC_MESSAGE, "Error: Cannot write non-volatile data, because Flash support has been disabled!\n");
#endif
}

void Platform::SetAutoSave(bool enabled)
{
#ifdef FLASH_SAVE_ENABLED
	autoSaveEnabled = enabled;
#else
	Message(GENERIC_MESSAGE, "Error: Cannot enable auto-save, because Flash support has been disabled!\n");
#endif
}

// Send beep message to the AUX device
void Platform::Beep(int freq, int ms)
{
	MessageF(AUX_MESSAGE, "{\"beep_freq\":%d,\"beep_length\":%d}\n", freq, ms);
}

// Note: the use of floating point time will cause the resolution to degrade over time.
// For example, 1ms time resolution will only be available for about half an hour from startup.
// Personally, I (dc42) would rather just maintain and provide the time in milliseconds in a uint32_t.
// This would wrap round after about 49 days, but that isn't difficult to handle.
float Platform::Time()
{
	unsigned long now = micros();
	if (now < lastTimeCall) // Has timer overflowed?
	{
		addToTime += ((float) ULONG_MAX) * TIME_FROM_REPRAP;
	}
	lastTimeCall = now;
	return addToTime + TIME_FROM_REPRAP * (float) now;
}

void Platform::Exit()
{
	Message(GENERIC_MESSAGE, "Platform class exited.\n");
	active = false;
}

Compatibility Platform::Emulating() const
{
	if (nvData.compatibility == reprapFirmware)
		return me;
	return nvData.compatibility;
}

void Platform::SetEmulating(Compatibility c)
{
	if (c != me && c != reprapFirmware && c != marlin)
	{
		Message(GENERIC_MESSAGE, "Error: Attempt to emulate unsupported firmware.\n");
		return;
	}
	if (c == reprapFirmware)
	{
		c = me;
	}
	if (c != nvData.compatibility)
	{
		nvData.compatibility = c;
		if (autoSaveEnabled)
		{
			WriteNvData();
		}
	}
}

void Platform::UpdateNetworkAddress(byte dst[4], const byte src[4])
{
	bool changed = false;
	for (uint8_t i = 0; i < 4; i++)
	{
		if (dst[i] != src[i])
		{
			dst[i] = src[i];
			changed = true;
		}
	}
	if (changed && autoSaveEnabled)
	{
		WriteNvData();
	}
}

void Platform::SetIPAddress(byte ip[])
{
	UpdateNetworkAddress(nvData.ipAddress, ip);
}

void Platform::SetGateWay(byte gw[])
{
	UpdateNetworkAddress(nvData.gateWay, gw);
}

void Platform::SetNetMask(byte nm[])
{
	UpdateNetworkAddress(nvData.netMask, nm);
}

void Platform::Spin()
{
	if (!active)
		return;

	// Write non-blocking data to the AUX line
	if (auxOutputBuffer != nullptr)
	{
		size_t bytesToWrite = min<size_t>(Serial.canWrite(), auxOutputBuffer->BytesLeft());
		if (bytesToWrite > 0)
		{
			Serial.write(auxOutputBuffer->Read(bytesToWrite), bytesToWrite);
		}

		if (auxOutputBuffer->BytesLeft() == 0)
		{
			auxOutputBuffer = reprap.ReleaseOutput(auxOutputBuffer);
		}
	}

	// Write non-blocking data to the second AUX line
	if (aux2OutputBuffer != nullptr)
	{
		size_t bytesToWrite = min<size_t>(Serial1.canWrite(), aux2OutputBuffer->BytesLeft());
		if (bytesToWrite > 0)
		{
			Serial1.write(aux2OutputBuffer->Read(bytesToWrite), bytesToWrite);
		}

		if (aux2OutputBuffer->BytesLeft() == 0)
		{
			aux2OutputBuffer = reprap.ReleaseOutput(aux2OutputBuffer);
		}
	}

	// Write non-blocking data to the USB line
	if (usbOutputBuffer != nullptr)
	{
		if (!SerialUSB)
		{
			// If the USB port is not opened, free the data left for writing
			OutputBuffer *buffer = usbOutputBuffer;
			usbOutputBuffer = nullptr;

			do {
				buffer = reprap.ReleaseOutput(buffer);
			} while (buffer != nullptr);
		}
		else
		{
			// Write as much data as we can...
			size_t bytesToWrite = min<size_t>(SerialUSB.canWrite(), usbOutputBuffer->BytesLeft());
			if (bytesToWrite > 0)
			{
				SerialUSB.write(usbOutputBuffer->Read(bytesToWrite), bytesToWrite);
			}

			if (usbOutputBuffer->BytesLeft() == 0)
			{
				usbOutputBuffer = reprap.ReleaseOutput(usbOutputBuffer);
			}
		}
	}

	// Diagnostics test
	if (debugCode == DiagnosticTest::TestSpinLockup)
	{
		for (;;) {}
	}

	ClassReport(longWait);
}
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

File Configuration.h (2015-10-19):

/****************************************************************************************************

RepRapFirmware - Configuration

This is where all machine-independent configuration and other definitions are set up.  Nothing that
depends on any particular RepRap, RepRap component, or RepRap controller  should go in here. Define
machine-dependent things in Platform.h

-----------------------------------------------------------------------------------------------------

Version 0.1

18 November 2012

Adrian Bowyer
RepRap Professional Ltd
http://reprappro.com

Licence: GPL

****************************************************************************************************/

#ifndef CONFIGURATION_H
#define CONFIGURATION_H

#define NAME "RepRapFirmware"
#define VERSION "1.1"
#define DATE "2015-10-15"

#define AUTHORS "reprappro, dc42, chrishamm, t3p3, dnewman"

// Comment out the following line if you don't want to build the firmware with Flash save support
#define FLASH_SAVE_ENABLED

// Other firmware that we might switch to be compatible with.

enum Compatibility
{
	me = 0,
	reprapFirmware = 1,
	marlin = 2,
	teacup = 3,
	sprinter = 4,
	repetier = 5
};

// Generic constants

static const float ABS_ZERO = -273.15;						// Celsius
static const float NEARLY_ABS_ZERO = -273.0;				// Celsius
static const float ROOM_TEMPERATURE = 21.0;					// Celsius

static const float INCH_TO_MM = 25.4;
static const float MINUTES_TO_SECONDS = 60.0;
static const float SECONDS_TO_MINUTES = 1.0 / MINUTES_TO_SECONDS;

static const float LONG_TIME = 300.0;						// Seconds
static const float MINIMUM_TOOL_WARNING_INTERVAL = 4.0;		// Seconds

// Heater values

static const float HEAT_SAMPLE_TIME = 0.5;					// Seconds
static const float HEAT_PWM_AVERAGE_TIME = 5.0;				// Seconds

static const float TEMPERATURE_CLOSE_ENOUGH = 2.5;			// Celsius
static const float TEMPERATURE_LOW_SO_DONT_CARE = 40.0;		// Celsius
static const float HOT_ENOUGH_TO_EXTRUDE = 160.0;			// Celsius
static const float HOT_ENOUGH_TO_RETRACT = 90.0;			// Celsius
static const float TIME_TO_HOT = 150.0;						// Seconds

static const uint8_t MAX_BAD_TEMPERATURE_COUNT = 6;			// Number of bad temperature samples before a heater fault is reported
static const float BAD_LOW_TEMPERATURE = -10.0;				// Celsius
static const float BAD_HIGH_TEMPERATURE = 300.0;			// Celsius

// Default Z probe values

static const size_t MAX_PROBE_POINTS = 16;					// Maximum number of probe points
static const size_t MAX_DELTA_PROBE_POINTS = 8;				// Must be <= MaxProbePoints, may be smaller to reduce matrix storage requirements. Preferably a power of 2.

static const float DEFAULT_Z_DIVE = 5.0;					// Millimetres
static const float DEFAULT_PROBE_SPEED = 2.0;				// Default Z probing speed
static const float DEFAULT_TRAVEL_SPEED = 100.0;			// Default speed for travel to probe points

static const float TRIANGLE_ZERO = -0.001;					// Millimetres
static const float SILLY_Z_VALUE = -9999.0;					// Millimetres

// String lengths

static const size_t LONG_STRING_LENGTH = 1024;
static const size_t FORMAT_STRING_LENGTH = 256;
static const size_t SHORT_STRING_LENGTH = 40;

static const size_t GCODE_LENGTH = 100;
static const size_t GCODE_REPLY_LENGTH = 2048;
static const size_t MESSAGE_LENGTH = 256;

// Output buffer lengths

static const uint16_t OUTPUT_BUFFER_SIZE = 256;				// How many bytes does each OutputBuffer hold?
static const size_t OUTPUT_BUFFER_COUNT = 16;				// How many OutputBuffer instances do we have?

// Move system

static const float DEFAULT_FEEDRATE = 3000.0;				// The initial requested feed rate after resetting the printer
static const float DEFAULT_IDLE_TIMEOUT = 30.0;				// Seconds

// Print estimation defaults

static const float NOZZLE_DIAMETER = 0.5;					// Millimetres
static const float FILAMENT_WIDTH = 1.75;					// Millimetres
static const size_t MAX_LAYER_SAMPLES = 5;					// Number of layer samples for end-time estimation (except for first layer)
static const float ESTIMATION_MIN_FILAMENT_USAGE = 0.025;	// Minimum per cent after which the first layer height is determined
static const float FIRST_LAYER_SPEED_FACTOR = 0.25;			// First layer speed factor compared to other layers (only for layer-based estimation)

// Webserver defaults

static const char *DEFAULT_PASSWORD = "reprap";				// Default machine password
static const char *DEFAULT_NAME = "My Duet";				// Default machine name

static const char *INDEX_PAGE_FILE = "reprap.htm";
static const char *FOUR04_PAGE_FILE = "html404.htm";

// Filesystem and upload defaults
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

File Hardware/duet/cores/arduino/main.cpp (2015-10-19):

/*
  main.cpp - Main loop for Arduino sketches
  Copyright (c) 2005-2013 Arduino Team.  All right reserved.

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
  You should have received a copy of the GNU Lesser General Public
  License along with this library; if not, write to the Free Software
  Foundation, Inc., 51 Franklin St, Fifth Floor, Boston, MA  02110-1301  USA
*/

#define ARDUINO_MAIN
#include "Arduino.h"

/*
 * Cortex-M3 Systick IT handler
 */
/*
extern void SysTick_Handler( void )
{
  // Increment tick count each ms
  TimeTick_Increment() ;
}
*/

// Weak empty variant initialization function.
// May be redefined by variant files.
void initVariant() __attribute__((weak));
void initVariant() { }

/*
 * \brief Main entry point of Arduino application
 */
int main( void )
{
	// Initialize watchdog
	watchdogSetup();
	
	init();

	initVariant();

	delay(1);

#if defined(USBCON)
	USBDevice.attach();
#endif

	setup();

	for (;;)
	{
		loop();
		if (serialEventRun) serialEventRun();
	}

	return 0;
}

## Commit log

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2014-04-16 Version 66. The tool class has been fully implemented. This compiles without errors, but it has not been tested and will probably not work. Use the previous or the next commit.
    [Configuration.h]
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2014-04-20 Fixed bug whereby two (or more) tools sharing (a) common heater(s) would not set their temperatures correctly on being selected.
    [Configuration.h]
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2014-05-08 Fixed compatibility between the Webserver class and reprap.js so that multiple temps don't get read as X Y Z etc.
    [Heat.cpp]
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2014-06-03 Version 0.75
    Removed ftoa function - all floating point o/p now done using snprintf.
    Removed short char scratch arrays from Webserver class - now uses the global scratchString throughout.
    Removed the extruder-only array of Pythagorean distances per step. Now all Pythagorean distances
    are stored for all drives in one array for all possible combinations (256 of 'em...). N.B this goes
    up by one power of 2 for each drive added, and - in practice - contains a lot of duplicated information
    when the steps/mm values for different drives are equal. It should be possible to compress this.
    Removed distributed calls to the Web reply function throughout the code that send messages to the
    web interf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
    [Configuration.h]
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2014-06-08 Version 0.77
    Passes release tests.
    At-temperature band relaxed slightly from 2 C to 3 C.
    Defauls PID I values changed from 0.027 to 0.5 for faster warm-up and better temp. control.
    Standby code changed so it doesn't do anything with unused heaters.
    Allow bed standby temp. to be set with M140 R30 etc.
    Functions dealing with transformed and untransformed coordinates sorted out and given better names in Move.
    Look-ahead lengthened from 7 moves to 20.
    [Configuration.h, coathook.g, config.g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]
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2014-06-11 Version 0.78
    Fixed bug whereby doing a G92 failed to set the speeds correctly for the
    start of the next move (i.e. it failed to acknowledge that - when a G92 is
    done - the machine must be stationary).
    [Configuration.h, homex.g]
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2014-06-16 Version 0.79
    Divided the action taken on G, M and T codes into three separate
    functions, as suggested by dc42. This allows M to be done first
    which eliminates the bug when filenames have an upper case G in
    them.
    [Configuration.h]
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2014-06-18 Fixed small typo - M305 was M304... It is now M305 correctly.
    [GCodes.cpp]
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2014-06-24 Version 0.86
    IMPORTANT: with this version the direction of the Ormerod X axis is
    deliberately reversed. This means that the colour ordering of the
    X axis wires on the Duet board is now the same as that for all the
    other axes.
    If you upgrade to this and subsequent versions from Version 0.85 or
    a previous one, you will need to swap your X wires.
    This upgrade also implements the M569 (Set axis direction values)
    M code, so you can set the logical values that decide all axis directions.
    [Configuration.h]
2014-07-01 Version 0.87
    Heater timeouts implemented. If a heater doesn't get to temperature in a given
    time, it cuts out. The time is currently set to 120s. The hot bed (which takes a
    long time to warm) is currently not timed.
    [Configuration.h]
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2014-07-09 Removed "M558" calls from homing g-code files and changed some feed rates Messages printed to Telnet work again due to better memory utilisation Fixed network output for "M503" for bigger config file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
    [homeall.g, homex.g, homey.g]
2014-07-10 Version 0.78b-zpl FTP file lists can now use multipe send buffers to fix a bug where file lists were truncated Increased available RAM by another 2KB
    [Configuration.h]
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2014-07-15 Merged in changes for RRP's firmware 0.86 Note: Due to these changes the X axis will get inverted. The connector on the Duet has to be turned around for this FW to work.
    [Configuration.h]
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2014-07-16 Version 0.89a Merged in changes from dc42's firmware 0.78c M302 requires "P" parameter to allow/deny cold extrudes, it will only report the status otherwise Added "X" parameter to M558 to allow the u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
    [Configuration.h, homeall.g, homex.g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]
2014-07-18 Version 0.89b Merged in changes from 0.78d-dc42 (thanks once more, dc42!) Modified parts of the webserver to return cached file information about the file being printed and to return only one decimal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
    [Configuration.h]
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2014-07-20 Lowered cold extrusion temperature to 160C Decreased Z dive height for G32 to 5mm G90/G91 don't set absolute or relative extrusion any more Added workaround for an acceleration bug in the Move code M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
    [Configuration.h]
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2014-08-20 Version 0.89e-zpl Merged in changes from 0.78j-dc42 and 0.78k-dc42 Platform::Message and Platform::AppendMessage now accept variable arguments Potential bug fixes in the Move class Enabled -O3 GCC op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
    [Configuration.h, config.g]
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2014-08-26 Version 0.89f-zpl Merged in changes from dc42's latest firmware build Built firmware binary with -O3 optimization Bug fix: Filament usage is read from both start and end of a g-code file
    [Configuration.h]
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2014-08-31 Version 0.89g-zpl Merged in changes from dc42's firmware 0.78o-0.78q (thanks dc42) Separated Arduino patches for 1.5.4 and 1.5.6_r2 Bug fixes in the Webserver code (thanks dc42) Removed P parameter f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
    [Configuration.h]
2014-09-01 Version 0.89h Fixed acceleration bug once and for all (hopefully) File information can now be read completely from files generated by both Slic3r and Cura
    [Configuration.h]
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2014-09-09 Version 0.89i-zpl
    Merged in changes from dc42's latest firmware 0.78r
    Implemented cold retracts (minimum temperature is 90°C)
    G28 and M1 reset homed axes
    M0 does no longer disable any drives, M1 still does
    Implemented internal G-Code queue to execute codes in-time
    When prints are paused, moves stop after the current move completes
    Other minor changes
    [Configuration.h]
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2014-09-15 Version 0.89j-zpl
    Merged in changes from dc42's 0.78s firmware (except for his experimental LCD code)
    Homing G1 (G1 S1) sets position depending on the move direction
    Minor corrections
    [Configuration.h]
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2014-09-27 Version 0.89k
    Merged in dc42's latest bug fixes, but not tested yet
    [Configuration.h]
2014-10-06 Version 0.89m-zpl
    Merged in dc42's latest changes from his 0.78t release (thanks dc42)
    Fixed cold extrusion/retraction for first few extruding moves
    [Configuration.h, config.g, tfree1.g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]
2014-10-15 Version 0.96a-zpl
    Merged in most of RRP's new firmware features from 0.90-0.96:
    - G32 runs /sys/bed.g if it exists (file doesn't have to be present with my fork)
    - Ormerod 2 compatibility and different SD card images
    - File print progress reported to web interface
    - Duet v0.7 support (experimental)
    - Network can be disabled (M552 S0)
    INFO: The probe index of dc42's ultrasonic sensor had to change from 3 to 4 to stay compatible with RRP's firmware
    Bug fix: Actual extruder positions are reported instead of internal ones used by the GCodes class
    Improved code queuing and added more safety precautions
    Updated README file to incorporate Network class and to mention my changes
    [Configuration.h, circle.g, coathook.g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]
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2014-10-25 Version 0.96b
    - M82 and M83 no longer reset the reported extruder positions
    - Moved print factor implementation (extrusion+speed) to the Move class
    - GCodes: All codes will report replies with a '\n' at the end
    - Calling M106 with no arguments reports current fan value in per cent
    - M112 (Emergency Reset) doesn't send a reply to the web interface
    - Webserver reports raw extruder positions without any modifiers applied to improve filament-based estimation.
    This also fixes a bug where the web interface would report incorrect filament-based progress if Cura G-Code files with
    more than 10000mm filament usage were printed (Cura generates G92 to reset it).
    - Current fan value is reported to th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
    [Configuration.h]
2014-11-09 Version 0.96c-zpl
    Updated Arduino toolkit to 1.5.8 (patches can be found in ArduinoCorePatches)
    - Merged in more of RRP's dev firmware 0.94 to be able to build the firmware again (thanks Adrian)
    Code queue items are allocated on start-up, dynamic allocation is no longer used
    Removed some redundant code (Platform::SetZProbing, HEAD_OFFSETS)
    Code checks for code queueing improved and added proper description for design principles
    M0 only turns off all drives and heaters if the print is NOT paused, although current tool is deselected at all times
    GCodes: Replaced Platform::Message calls with reply.copy where applicable
    Requirement to specify all the extruders for M92, M201, M203, M566 and M906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
    [Configuration.h]
2014-11-10 Minor changes (no code logic has changed)
    Renamed two methods in the Network class to make more sense
    Platform: IP address, subnet mask and gateway are returned as "unsigned char" to fix Eclipse code analysis errors
    [Network.h, Platform.h]
2014-11-18 Version 0.96d-zpl
    Added code for internal UART line to add support for external devices (thanks dc42)
    Implemented M105 S2 to output JSON status message (thanks dc42)
    Updated dc42's and my list of firmware changes
    M0 no longer deselects the current tool when a print is paused
    Implemented M32 (Select file and start SD print)
    When a paused print is resumed, M24 (Resume print) runs "resume.g" and goes back to the position the print was originally paused at
    M25 (Pause print) runs "pause.g" file and slows down the current move
    Implemented isolated moves in the Move code. These will be performed if the look-ahead can't be used, e.g. because a print has been paused
    Move code recalculates acceleratio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
    [Configuration.h, pause.g, resume.g]
2014-11-20 Version 0.96e
    Implemented M26 and M400
    Improved the way Move checks for extruder capabilities
    Fixed M220 (speed factor override) again
    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
    [Configuration.h]
2014-11-22 Intermittent commit
    M0 now runs reset.g and doesn't disable any drives any more (again)
    M81 disables drives before ATX power is turned off
    Bug fix: Aux G-codes are executed immediately when a print is in progress
    Bug fix: FileStore::Seek didn't set internal bytesRead property
    Bug fix: Disabled code queue for M105 for Pronterface
    Increased Z lift in homeall files from 2mm to 3mm
    Adjusted center probe position in homeall and homez files
    Rearranged SD-image directories to look equal to the ones in dc42's firmware fork
    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
    [Configuration.h, circle.g, coathook.g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]
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2014-11-30 Version 0.96f-zpl
    - Modified code queue to store only a few codes and reduced its memory usage
    - Implemented M226 (GCode initiated Pause)
    - Rewrote most of the Move::Spin call and implemented split moves for 5-point bed compensation
    - Improved Pause/Resume/Reset feature and parts of the networking code
    - Removed some more redundant code
    - Last message is now stored in Flash (may be useful for debugging)
    - Bug fix: M120+M121 now save and restore the last-known extruder positions
    - Bug fix: Possible endless loop in the Network code
    - Other minor changes
    Thanks to dc42 for the following:
    - Initializing arrays using ARRAY_INIT macro
    - Fixed issue where the active aux GCodeBuffer could become ov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
    [Configuration.h]
2014-12-02 Version 0.96g
    - Implemented 'R' paramter for G0/G1 to be able to go to the coordinates a print was initially paused at
    - Added 'R' parameter to M106 to restore the last-known fan value
    - Implemented proper LWIP locks to get rid of some networking glitches
    - Network class now utilizes ClassReport as all other classes do
    - Adjusted resume and pause macros to use the new "G1 R1" feature
    - Increased FTP and HTTP upload performance a bit
    - Bug fix: Fraction of file printed returns correct value when a print is being resumed
    - Bug fix: Code queue will run next item if another code shall be queued and there is no more space available (fixes potential freeze issue)
    - Bug fix: Fixed issue where some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
    [Configuration.h, pause.g, resume.g]
2014-12-03 Version 0.96h
    Bug fix: Wrong extruder values were passed to the web interface when 5-point bed compensation was used
    [Configuration.h]
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2014-12-10 Version 0.96i
    - The web inteface won't report a file is being printed when a single macro file is being executed, unless it's called from a real G-Code file
    - Cleaned up some parts of the networking code
    - debugPrintf does no longer allocate memory dynamically
    - Bug fix: When a print is cancelled, the right (untransformed) coordinates will be set
    - Bug fix: Fixed an issue where some moves were occasionally ignored by the Move class
    [Configuration.h]
2015-01-06 Intermediate commit
    - Merged in dc42's changes up to 0.78za (thanks dc42!)
    - Moved status response code entirely to RepRap class
    - Dropped support for old web interfaces
    - Implemented password protection in the HTTP server
    - Added custom code to M117 and M300 for new web interface
    - Bug fix: Pause macro isn't executed when M25 is called twice
    - Bug fix: Finally fixed occasional "Lost data connection" bug in FTP server
    - Minor changes
    [Configuration.h]
2015-01-10 Reverted M105 code and introduced new field
    Introduced extra field called "probeSecondary" in status response
    [GCodes.cpp, RepRapFirmware.cpp]
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2015-01-17 Version 0.96k-alpha
    New JSON status responses as suggested on the RepRap wiki are now fully working
    Implemented firmware-based print time estimations
    Before a printing file is closed, DoFileMacro waits for all moves to finish first
    M98 allows absolute paths, so files from directories other than /sys can be run
    Improved print status detection and simplified pause code
    Fixed issue where rr_fileinfo returned an error when called for a directory
    Preparations for new JSON config response
    Merged in old-style JSON status response code from dc42's fork for M105
    Fixed issue where RepRap::GetFilesResponse returned invalid JSON responses for empty directories
    "ok" replies for Telnet clients are followe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
    [Configuration.h]
2015-01-19 More changes
    Merged in dc42's improved Flash code and parts of his diagnostics changes (thanks dc42)
    Removed className parameter from ClassReport, because I don't need it any more
    M122 reports the last-known spinning class after a Spin timeout occured
    Implemented additional diagnostics test
    Flash error messages now end with a NL
    Moved LWIP's stats_display call from Platform to Network
    Made HTTP password authentication optional again
    Webserver doesn't report debug messages via DEBUG_MESSAGE any more
    [Configuration.h]
2015-01-29 Version 0.96k
    Merged in more non-Move related changes from dc42's fork (thanks again)
    Moved generic string length definitions to Configuration.h
    Implemented M558 R-parameter and got rid of RRP's newly introduced probe index 3
    Added geometry field to my webserver JSON status response
    Fixed issue where 'C' state wasn't reported in old-style JSON status response
    Bug fix: filenameBeingUploaded was not actually set when an upload was initiated
    [Configuration.h]
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2015-02-02 Version 1.04 ------------
    Fixed bug in the Move class cosine() function whereby it didn't deal correctly
    with absolute axis and relative extruder moves. Should fix occasional funny movement
    problems...
    [Configuration.h]
2015-02-16 Version 1.05 ------------
    Bug in reporting tempereatures to Pronterface fixed. Also
    temperatures will continue to be reported even when a heater
    develops a fault.
    Made a start on automating the setup of the machine. The SD-image
    folder now contains setups for all the main models and variants and
    a README on which files to copy and how.
    These variants need to be tested.
    [2colour.g, Configuration.h, bed.g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]
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2015-02-26 Version 0.96l-zpl
    Implemented offsets for 'G1 R1' as seen in dc42's fork
    M117 and M300 now benefit from the code queue
    Merged in improved LookAhead::Cosine method from RRP's dev branch
    Moved print-related code to new PrintMonitor class
    Merged in dc42's status response changes for the PanelDue
    Introduced new "type" key for rr_upload_begin to optionally disable UTF-8 checks
    Cleaned up some more code in the Webserver class
    Bug fix: Some users could not load the web interface due to too low SNDBUF length
    Bug fix: M23 doesn't set the print start time, this one is set by M24 instead
    Bug fix (temporary): Increased JSON response buffer length back to 2KB
    [Configuration.h]
2015-02-27 Version 0.96m-zpl
    Implemented nested macros
    Response sequence number is increased on every Message call
    Implemented 'R' parameter for M105 (for PanelDue)
    Bug fix: bed.g was not called even if it existed
    Bug fix: M105 status responses report G-Code responses (and error messages) for PanelDue
    [Configuration.h]
2015-03-05 Version 0.96n-zpl
    Implemented POST uploads and rr_move request
    Hostname is announced in DHCP requests (experimental)
    Bug fix: No filament values are reported if file info wasn't detected
    Bug fix: Webserver doesn't crash any more if too many header values were passed
    Bug fix: FTP RNFR+RNTO commands allow files to be moved (for FileZilla)
    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
    [Configuration.h]
2015-03-09 Version 1.08 ------------
    Fixed bug whereby fractional parts of steps/mm were being reported with either too many or no decimal places...
    [Configuration.h]
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2015-03-11 Small bug fixed in M92 command (removed (int) casts on steps/mm reporting - M92). Also a T command on its own reports the currently selected tool (if any).
    [GCodes.cpp]
2015-03-12 Fix bug in config.g
    Also updating GCodes to use T0 instead of T1
    [Coat Hook.g, HuxAxis.g, MendAxis.g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]
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2015-03-23 Version 1.08a
    Merged in several improvements from dc42's fork (thanks dc42):
    - Support for M571, M573, M575 added
    - M906 sets motor idle currents (via 'I' parameter)
    - M0 puts drives into idle mode
    - More changes for GCodeBuffer class
    - HTTP port can be set using M552 R<port>
    - Minor corrections in the Network class
    - M0/M1 guarantee all heaters to be switched off
    - M0/M1 will send a response if a paused print is cancelled
    Merged in changes from RRP's dev branch up to v1.08 (thanks Adrian/RRP):
    - Changes of v1.06 are implemented using the code queue
    - Support for M144 added
    - T-code reports current tool if no number is specified
    - Temperatures are reported even if a heater fault occured
    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
    [Configuration.h]
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2015-03-24 Version 1.08b
    Expanded M105 response to report all heater temperatures (including their target temps)
    Cold extrude warning is reported whenever extrusion moves are prevented
    Bug fix: M25 could crash the firmware if no moves were performed before it is called
    Bug fix: Individual string buffer is used in CombineName for macro files
    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
    [Configuration.h]
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2015-03-27 bed.g file updated in test branch so that X doesn't move too far by default.
    [bed.g]
2015-03-30 Version 1.08c
    Merged SamNonDuePin library into Arduino core
    Implemented rr_config response
    Updated SD image directories from RRP's official files (with minor adjustments)
    Removed "reset.g" and added support for "stop.g" and "sleep.g"
    If M1 is called from the serial interface, M25 is run if Marlin is being emulated
    M25 runs "pause.g" only if no live movement is present
    M25 runs "resume.g" only if "pause.g" was executed before
    G1 S1 sets hit position depending on the homing move's direction
    Replaced ENABLE and DISABLE with ENABLE_DRIVE and DISABLE_DRIVE (thanks mike-o-tronic)
    G-Code response buffer is only cleared when it is actually polled (to view start-up errors from the web interface)
    Bug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
    [Circle.g, Configuration.h, Turn off E motors.g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]
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2015-03-31 Three more...
    Tool number adjustment is cleared whenever a new print starts
    PrintMonitor class provides new interface to get notified about stopped prints
    Bug fix: M1 is superseded by M25 only if the print was not paused before
    [GCodes.cpp]
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2015-04-16 Version 1.08d
    Moved tool number check to GCodes class (to prevent possible memory leak)
    Responses from macro files are no longer followed by "ok" if Marlin is emulated (ok will be reported as soon as the macro has finished)
    Modified M20 S2 to report directories with '*' prefix (useful for future PanelDue firmware versions)
    Implemented M116 C-parameter to wait for the chamber temperature to be reached
    Implemented M141 with additional 'H' parameter to specify the chamber heater to use
    Implemented M408 as described on the G-code wiki page (for future PanelDue firmware versions)
    PIDs may be turned on only if no heater fault occurred before
    Implemented safety feature to prevent too high heater te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
    [Configuration.h, bed.g, tpost0.g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]
2015-04-17 Version 1.08e
    Updated Ormerod bed.g files to call G30 S again after last point
    Bug fix: Motor currents were occasionally not updated when in idle mode
    [Configuration.h, bed.g]
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2015-04-24 Updates to SD image. Now there is just one image, to avoid duplication.
    [Calibration-140x140.g, Calibration-200x200.g, Calibration-new-60mm.stl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]
2015-04-26 Version 1.08f
    Z-probe ADC conversions are finished before different IR probe is used (also see RRP O2 homing files)
    ADC filters' Init routine may no longer be interrupted by IRQs (thanks dc42)
    First layer height is properly detected if a first layer height of 0.5mm is used
    Cold extrusion warning provides the tool number
    Updated O1+O2 config templates to set thermistor series resistor for second hot end
    Updated O1+O2 homing and bed levelling macros with positions suitable for my stock Ormerod 2
    Bug fix: Existing tools could not be deleted via M563 P# D-1 H-1
    Bug fix: M408 didn't return right response for types >= 2
    Bug fix: M906 returned the current values even if E currents were set
    Bug fix: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
    [Configuration.h, bed.g, default.g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]
2015-04-26 Updated v1.08f once again...
    ... to fix invalid warning message saying tool could not be driven
    [RepRapFirmware.cpp]
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2015-06-09 Version 1.09a-zpl
    Introduced new Makefile for Linux and OS X, and a basic PowerShell compile script for Windows
    - "make" and "make all" compile the firmware
    - "make upload" resets the Duet via 1200BPS touch (only *nix-based OSs) and uploads firmware binary via bossac
    - "make clean" purges the build directories
    - Designed for Arduino 1.6.4 in conjunction with my Arduino board files (see Hardware directory)
    Updated README file
    Implemented M404 (filament width and nozzle diameter)
    Added proper IsPrinting interface to PrintMonitor class
    M24/M32 use the stack when a new file print is being started
    M552 reports both the configured and actual IP addresses
    Merged in (potential) fix for modulated Z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
    [Configuration.h]
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2015-07-03 Version 1.09b-zpl
    Improved internal memory management and freed up another 4KB of RAM
    Removed entire Line class from Platform files and improved Message calls
    Expanded use of C++11 features and introduced more type safety for const values
    Implemented G-Code interleaving and hopefully full support for dc42's PanelDue
    Improved robustness of the HTTP webserver
    Marlin is now emulated for both Serial (USB) and Telnet clients
    Moved some fields from the RepRap class to other modules (cold extrusion, sequence numbers)
    Z-Probe X+Y offsets and dive heights are now configurable (thanks dc42)
    Introduced new M577 code to wait until an endstop is triggered
    Bug fix: M301/M304 didn't report correct I/D term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
    [Configuration.h]
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
